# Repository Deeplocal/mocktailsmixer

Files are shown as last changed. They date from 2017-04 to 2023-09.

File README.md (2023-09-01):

# Google Assistant SDK Demo: Mocktails Mixer Gizmology 2023


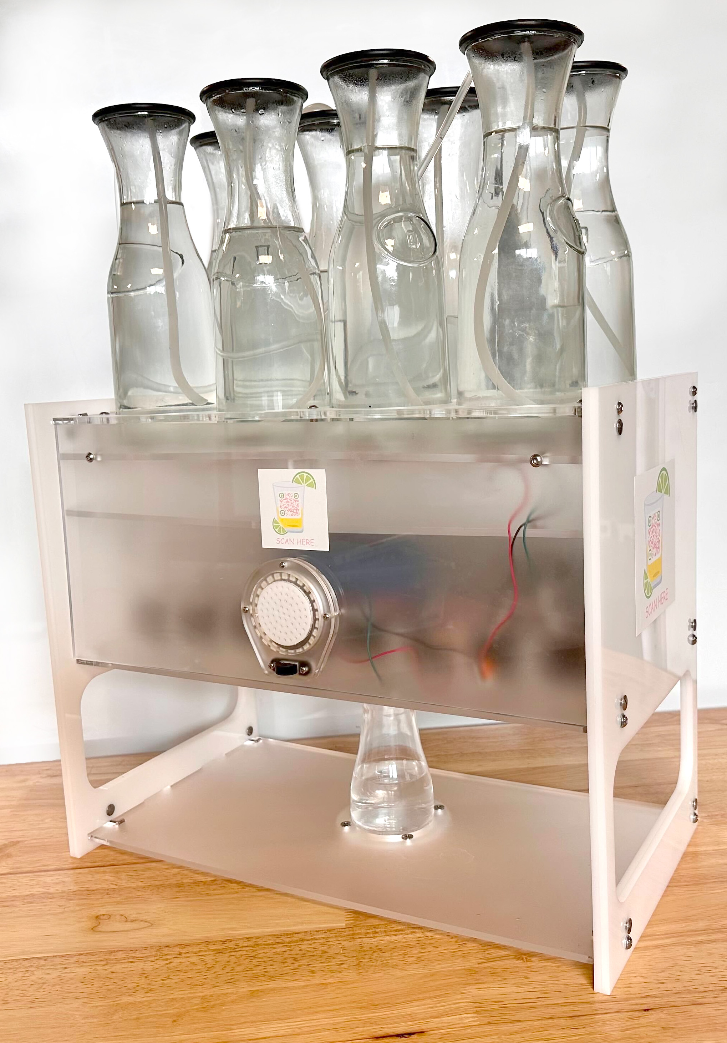
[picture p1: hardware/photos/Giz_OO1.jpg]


## Make a DIY robotic mocktails mixer with the Google Assistant built in.
##In the Spring of 2023, innovation studio and experiential design firm Deeplocal launched Gizmology, a one-year creative technology apprenticeship program for recent high school graduates and underemployed adults in Pittsburgh’s Black community. Supported in part by Deeplocal’s parent company WPP’s racial equity committments, Gizmology’s goal was to advance racial equity in creative and technical fields through on-the-job training and mentorship. Through an initial upfront classroom training spanning nearly four months the Gizmology apprentices, or Gizmos as they affectionately named themselves, learned the foundational skills related to 3D design, electrical engineering, physical computing, fabrication methods (laser cutting/welding/woodworking), and creative technology. Designed as two semesters, Gizmology 1 and Gizmology 2, each semester culminated with a capstone project; the final capstone for the classroom training was to ‘re-create’ a robotic mocktails mixer with Google Assistant built in. 

In mid-July, after weeks of interdisciplinary training and exposure, each of the Gizmos chose an apprenticeship track and set-out to complete the final capstone project fulfilling their specific roles. Jason focused on exhibit fabrication, Jordan delved deeper into technical integration, and Justin focused on Mechanical Design, with each pitching in to work as a team and support the assembly. For Creative Tech, Imani and Mecca shared the responsibility of updating and converting the SDK from Python to Node.Js as it was no longer valid; this was no small feat and an amazing accomplishment for a beginning creative technologist. For all the Gizmos, it was evident that the recreation of the robotic mocktails mixer with Google Assistant wasn’t simply going to be a matter of merely following directions, it was going to take creativity, ingenuity, and most importantly- the real world application of the skills they learned to successfully recreate the project as a team. What you’ll see below is the journey of the Gizmos to create the “Gizmology Mocktails Mixer”, complete with six uniquely designed mocktails (from eight different flavors) representing personal connections to each member of the Gizmology team. This DIY robotic home bartender whips up your favorite mixed drinks at your command–in the true spirit of the Gizmos!

**Disclaimer:** THESE INSTRUCTIONS ARE BEING PROVIDED FOR INFORMATIONAL PURPOSES ONLY AND ARE NOT INTENDED TO BE USED FOR THE PRODUCTION OF COMMERCIAL PRODUCTS.  BY EXECUTING THESE INSTRUCTIONS, YOU AGREE TO ASSUME ALL LIABILITY IN CONNECTION WITH YOUR BUILDING AND USE OF ANY DEVICE. DEEPLOCAL DISCLAIMS ALL WARRANTIES EXPRESS OR IMPLIED WITH RESPECT TO THESE INSTRUCTIONS AND ANY RESULTING DEVICE INCLUDING BUT NOT LIMITED TO WARRANTIES FOR MERCHANTABILITY, FITNESS FOR ANY PARTICULAR PURPOSE, AND NON-INFRINGEMENT.  YOU SHOULD USE EXTREME CAUTION WHEN BUILDING AND USING ANY DEVICE PURSUANT TO THESE INSTRUCTIONS.  IN NO EVENT SHALL DEEPLOCAL BE LIABLE FOR ANY CLAIM OR DAMAGES, INCLUDING BUT NOT LIMITED TO CLAIMS OR DAMAGES RELATED TO DEATH OR PERSONAL INJURY, PROPERTY DAMAGE, OR PRODUCT LIABILITY.

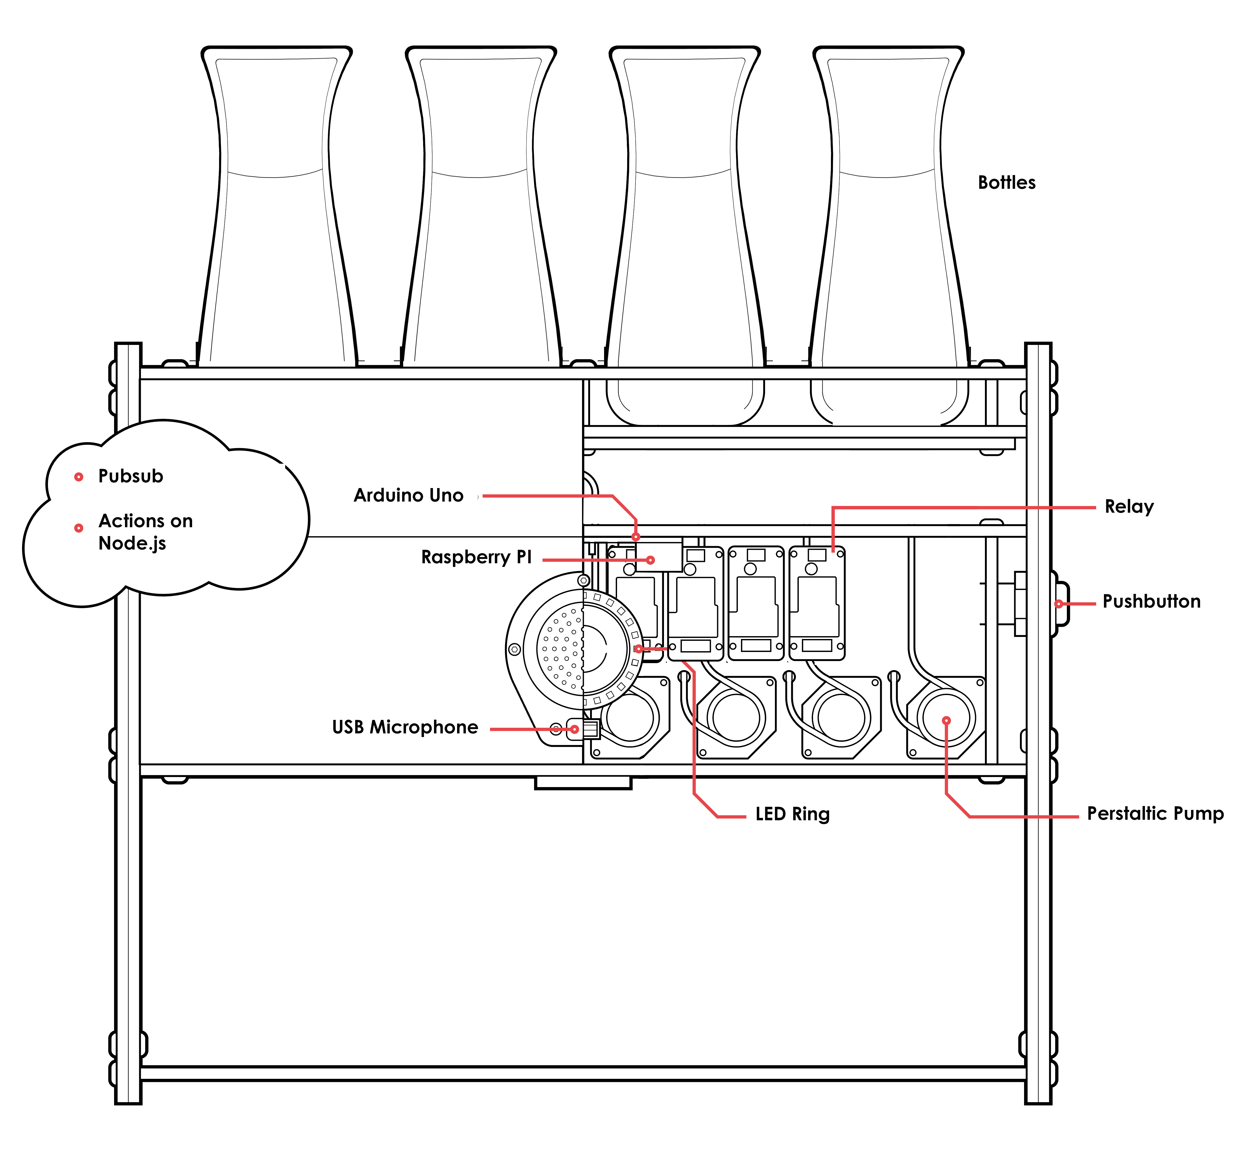
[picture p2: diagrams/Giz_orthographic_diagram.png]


**Features:**

- Voice-controlled drink ordering 
- Modular design allows you to customize your Mixer to include as many ingredients and drink combinations as you choose

## What You’ll Find
- diagrams/
- hardware/
  - cad/
  - laser-cut/
  - photos/
  - bill of materials
- software/
  - arduino/
  - rpi/
  - gcf/
  - api.ai agent zip

## What You'll Need
Before you get started, you should have a basic knowledge of soldering. You should also have access to a laser cutter.
You can find all of the parts we used, along with the exact quantity, supplier, cost, and links to purchase [here](hardware/bom.pdf).
Note: In general, we used parts that were readily available, but on the expensive side. This build could be completed with less expense if parts are sourced on Amazon/Alibaba or if lower quality parts are used.
Note: All materials used in this build are rated as “food safe.” Liquid does not come in contact with any material that is not food grade safe.

### Tools needed for the build are listed below:
- Hand drill
- Rubber mallet or hammer
- Screwdriver set
- X-ACTO knife
- Soldering Iron
- Wire cutters
- Wire strippers
- Scissors
- Hex Key Set
- Wrench Set

## Building the Mixer Body

### Step 1: Laser Cutting
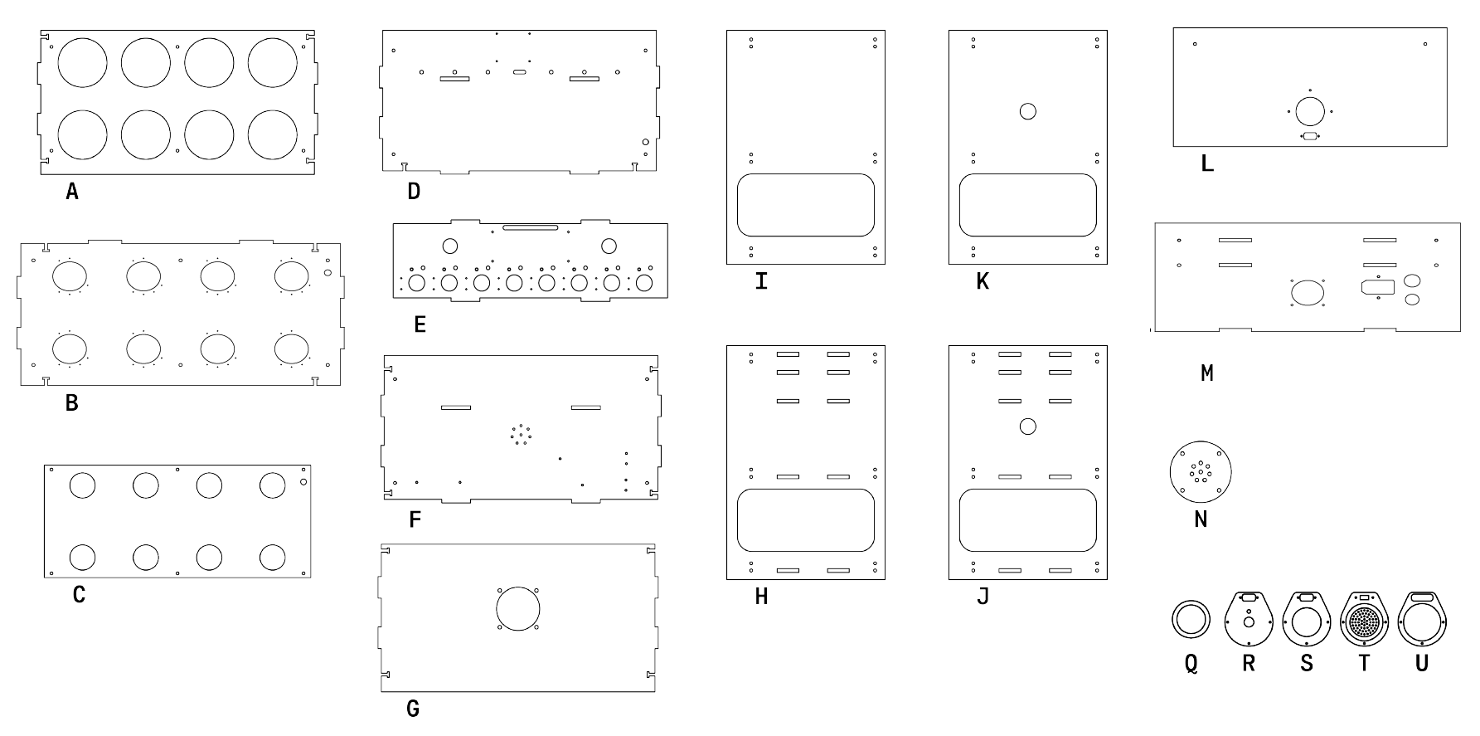
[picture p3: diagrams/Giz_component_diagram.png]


#### Laser cut all 2D profiles into the acrylic sheets.
Note: DFXs are all in inches. Please scale according to input of the laser cutter. See attached drawings for design guidance.
- A. Top Panel- ¼ inch thick
- B. Bottle Capture Panel- ¼ inch thick
- C. Lid Capture Panel- ¼ inch thick*
- D. Drip Panel- ¼ inch thick
- E. Pump-Relay Control Panel- ¼ inch thick*
- F. Pour Panel- ¼ inch thick
- G. Bottom Panel- ¼ inch thick
- H. Inside Side Panel- ¼ inch thick
- I. Outside  Side Panel-¼ inch thick
- J. Inside Side Button Panel-¼ inch thick
- K. Outside SIde Button Panel- ¼ inch thick
- L. Front Panel- ¼ inch thick
- M. Rear Panel- ¼ inch thick*
- N. Cup Indicator Panel- 1/16 inch thick
- O. Arduino Top Plate- 1/16 inch thick 
- P.  Arduino Bottom Plate- 1/16 inch thick
- Q. Speaker Diffusion Level
- R. Speaker Clear Level 16th- 1/16 inch thick
- S. Speaker Black Level 8th- ⅛ inch thick
- T. Speaker Black Level 8th 1- ⅛ inch thick
- U. Speaker Black Level 4th 1- ¼ inch thick

*Panels that were revised include:
Lid Capture Panel- needed holes for the light wire
Pump Relay Control Panel- CAD mount holes for brackets. CAD holes for wires from pumps to power and access for tubes to run through, holes for the relay to be mounted
Rear panel- CAD holes for mounting a fan 

*Note: We highly recomend a cardboard prototype. 

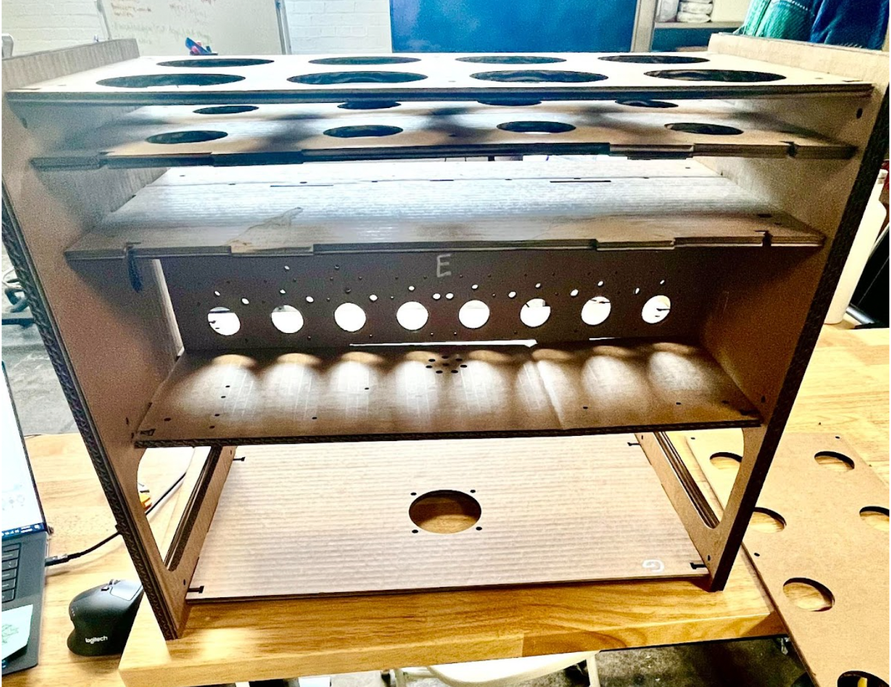
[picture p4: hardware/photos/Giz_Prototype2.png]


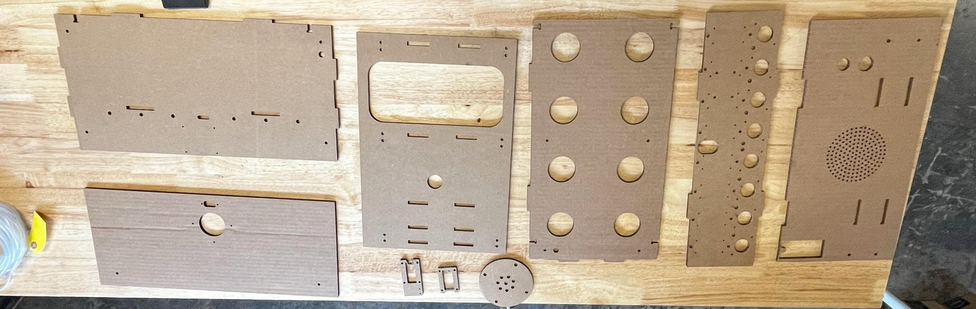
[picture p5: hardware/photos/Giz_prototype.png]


### Step 2: Assemble Bottle Holder Sub
Attach Top Panel with Bottle Capture Panel together with #10-32 x 1/2 inch length button socket cap and #10-32 x 1 inch length ¼ OD standoff.

On the other side, with Lid Capture Panel use 10-32 x ¾ inch length button socket cap fasteners (Optional - Double sided tape can be used to attach the Lid Capture Panel to the bottom of the Bottle Capture Panel).

Note: There is a ¼ inch overhang on the Top Panel. Rear panels are flush with the exception of the tabs.

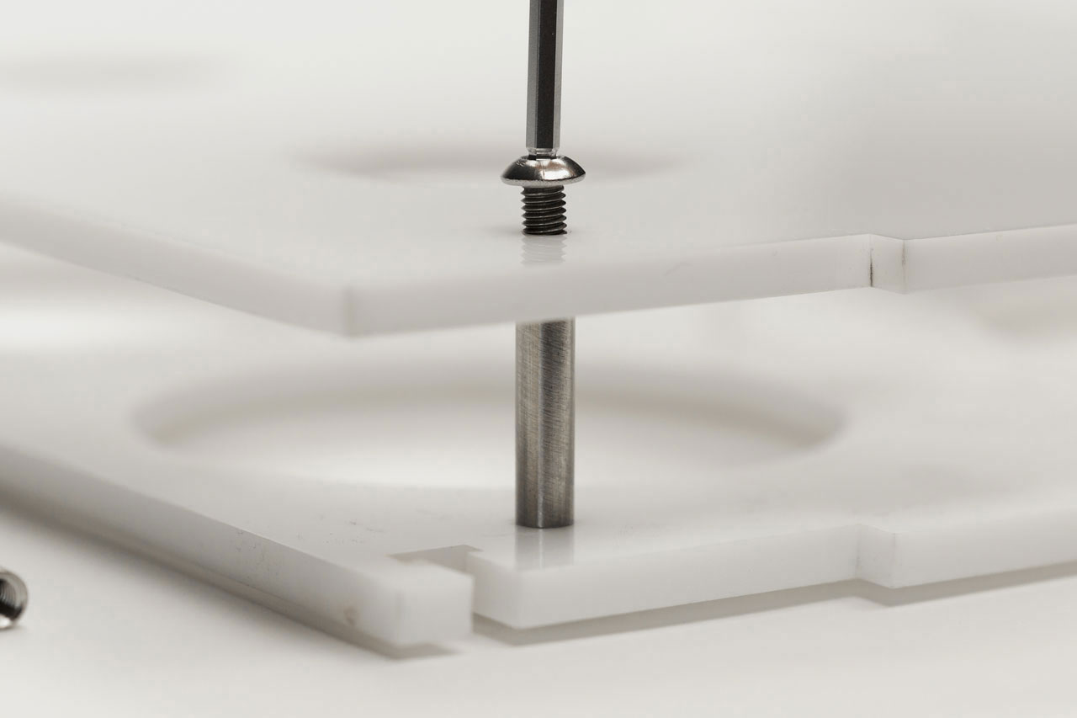
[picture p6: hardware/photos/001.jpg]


### Step 3: Assemble Pump and Relay Control Panel Sub
Note: To ensure pump tubing is food grade safe, please replace with Tygon Clear PVC tubing 3/32 inch ID x 5/32 inch OD (Hardness rating is “Soft” and durometer is 65A). The durometer is imperative to pump and tube life. This can be found on McMaster-Carr.

#### Install Food Grade Pump Tubing.
Remove cover from pumps by depressing snaps on both sides of pump head. Remove tubing that was placed in during shipment. Place food grade tubing into pump allowing 3 inches to remain outside the inlet and outlet of the pump. Also, be careful to not puncture the tubing when installing around the rollers.

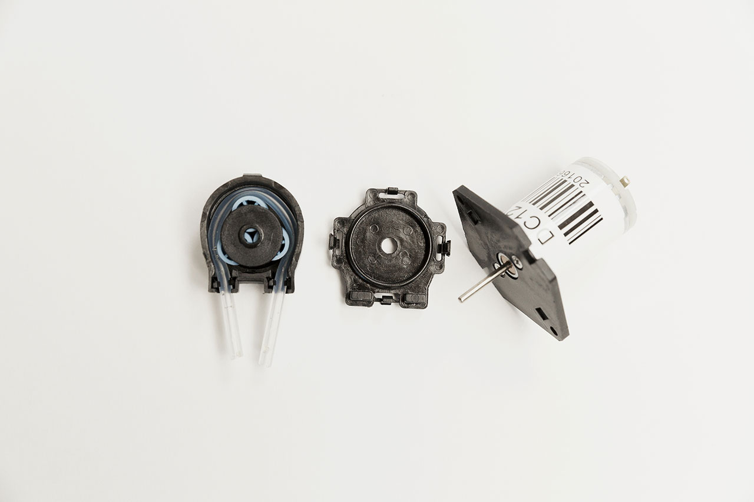
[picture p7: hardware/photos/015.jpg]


#### Attach Pumps.
The pumps that were available required brackets to be mounted. Brackets were created in solidworks and 3D printed. 

Use the Pump/Relay Control Panel and attach the brackets to the eight 1.10 inch diameter holes located on the panel. Place a #8 black rubber washer between the bracket and acrylic to reduce vibration.
Use a #2-56 x ½ inch length Phillips pan head machine screw and corresponding nut to fasten the brackets to the acrylic. Use the same screws and nuts to attach the pump to the bracket.

#### Attach Relay Module.
In this version, to save time, we have used an 8 channel
Relay module. Attach the 8-Channel Relay Module directly above each pump on the Pump/Relay Control Panel. There will be a 4 bolt hole pattern. Use the #2-56 x ⅜ inch length ⅛ inch OD standoffs (Optional - You can use #2-56 x 1/2 inch length Phillips pan head machine screw and corresponding nut instead of the standoffs.) with number #2 washers underneath each hole before the standoff. Fasten each corner with a #2-56 x 5/32 inch length Phillips pan head machine screw.  Note that the red led must be positioned toward the top of the acrylic sheet. Use a #2-56 x ⅜ inch length pan head Phillips machine screw and fasten relays from other side of acrylic.

Tip: When attaching the fasteners, washers and standoffs to the relay module, allow them to be loose. This will help with easy alignment to the corresponding holes on the acrylic than retighten fasteners on relays.

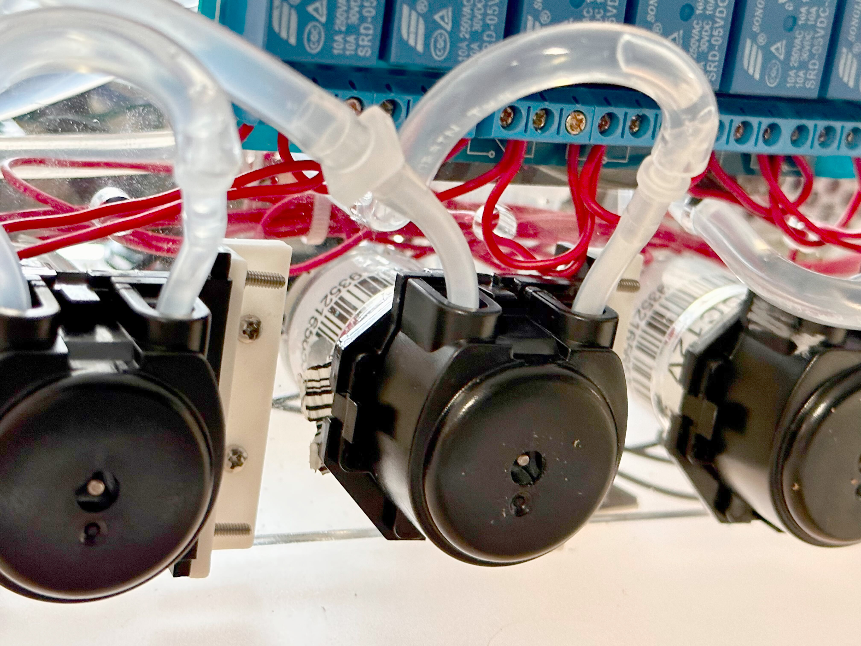
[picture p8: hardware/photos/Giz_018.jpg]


#### Attach Arduino Uno and Arduino Mount.
You can 3D print an Arduino Uno mount by using this link to download the file from GrabCAD. We used a Bambu Studio P1P 3D printer. The file takes about 6 minutes to print in total.

Place the Arduino on the mount, matching the holes on the Arduino to the corresponding holes on the mount. Use screws to secure the Arduino onto the mount. Attach the Arduino and the mount onto the back of the pump panel with VHB. You should leave enough room for the the wires from the relay to come through the slot and attach to the pins on the Arduino Uno.

#### Attach Raspberry Pi to Drip Panel.
Attach the Raspberry Pi to the back panel using velcore. 



## Wiring the Electrical System

#### Electrical System Overview



For a clearer view of the wiring diagram download the [fritzing file](diagrams/wiring_fritzing.fzz).

#### Control
The electrical system of the Mocktails Mixer uses two control systems. The first is a Raspberry Pi, which handles all of the communication with the Google Assistant SDK. The second is an Arduino Micro that controls the pumps and LEDs. Both of these systems are connected to each other over serial. The Raspberry Pi sends commands to the arduino about what lights and pumps to turn on and the Arduino executes them.

Outside of these two controllers, the Mocktails Mixer has four major hardware systems. They are Power, the Pumping system, Lights, and Audio.

#### Power
The power system controls the flow of electricity in the Mixer. However, the Mixer uses two different voltages: 12V for the pumps and 5V for the other hardware. You can handle this by using a step-down voltage regulator or a dual-voltage power supply. These are both adequate for the basic build of the Mixer, but if you want to add extra flair (like more LEDs),  you may need to use two separate power supplies. Our instructions and BOM use two power supplies.

Note: For safety, we recommend placing the power supply in an external enclosure to keep 110V away from the liquids in the mixer.

#### Pumps
In this version of the Mocktails Mixer, we used eight (8) peristaltic pumps. These are rated and recommended for use at 12V, but you can run them up to 24V if you find that the pumps are running too slow. The pumps are all individually switched by a relay controlled by the Arduino Uno.
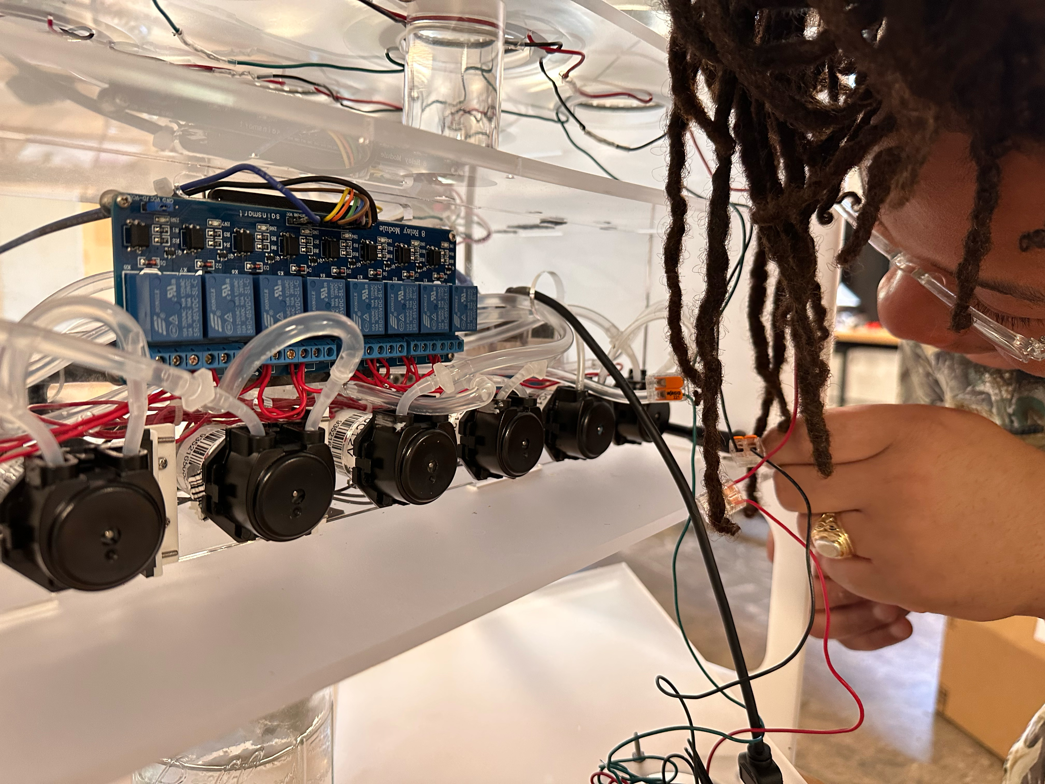
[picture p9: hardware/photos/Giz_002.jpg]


#### Lighting
For visual feedback, we added an LED ring to the Mixer. We used the Adafruit Neopixel. It is very easy to wire and add additional rings, plus the library is easy to use. These draw a decent amount to amperage, so if you want to add more to your build, you will need to size your 5V power supply accordingly.

#### Audio
Last but not least, we used a USB Microphone to speak and order drinks that is connected directly to the Raspberry Pi. We chose to not connect the speaker. If we did, the speaker could be connected to the amplifier on the Arduino’s mounting plate. The amplifier is connected to the Raspberry Pi via a 3.5 mm headphone jack.

## Electrical System Wiring Instructions

### Step 4: Wire the Power Supplies
To wire the power supply, first connect the AC Lines to their terminals (Black to L or Load, White to N or Neutral, Green to Ground). Next, connect the DC power lines to power supplies.
Note: To make the wiring easier to follow, we used red wire for all the 12V lines and green for all of the 5V lines. We kept the all of the Ground wires black because all devices will need to share Ground in order to communicate.
Note: We also recommend using a lower gauge wire (12 or 14 gauge), for the DC power lines moving from the power supply to the terminal block or the wire nut, then using a higher gauge (20 to 24 gauge) for all of the other lines.

Note: The pumps used in this assembly produce a lot of ground noise that can travel throughout the dinrail and could potentially interfere with communication between Raspberry Pi and Arduino to carry out commands properly. It is recommended that you add a 5k capacitor to the dinral with the long side going into the 12V supply and the short side going to ground to store the ground noise and resolve communication interference. 

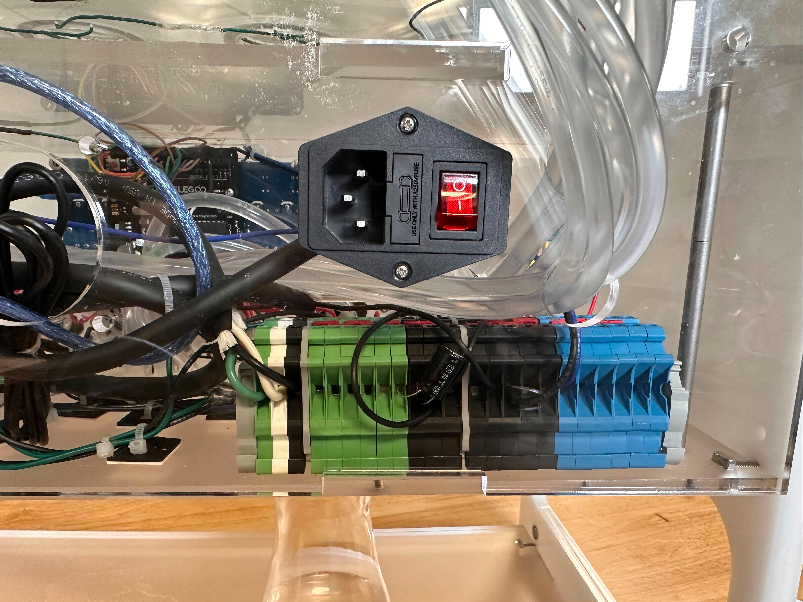
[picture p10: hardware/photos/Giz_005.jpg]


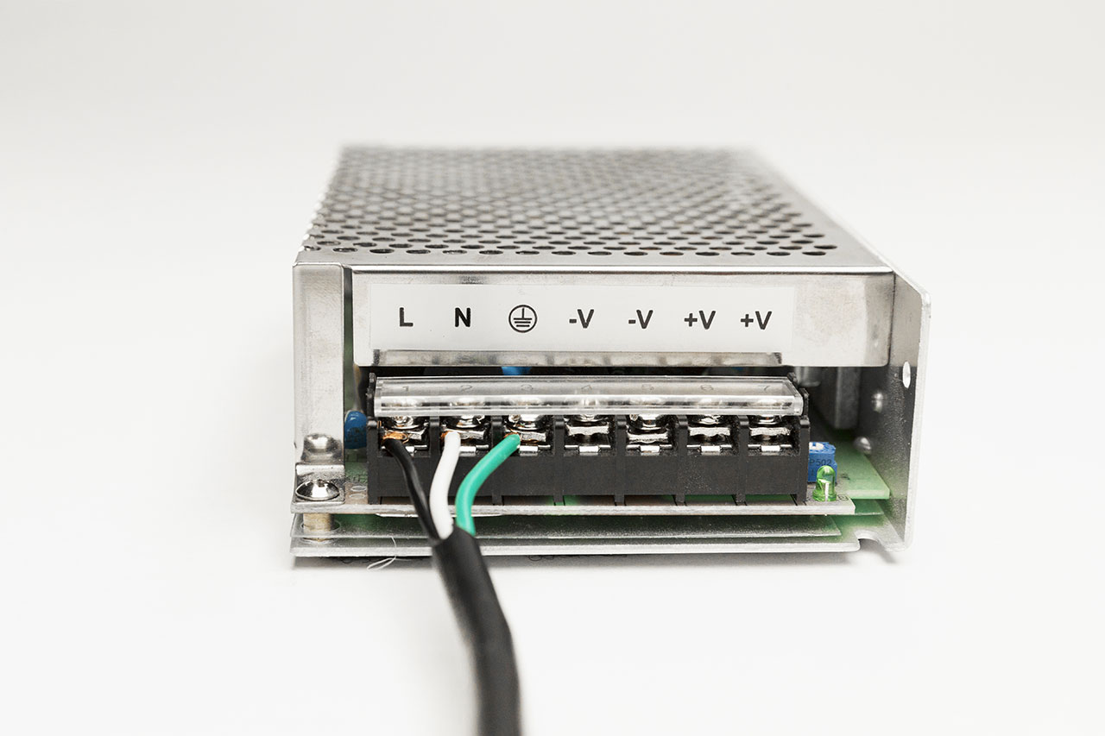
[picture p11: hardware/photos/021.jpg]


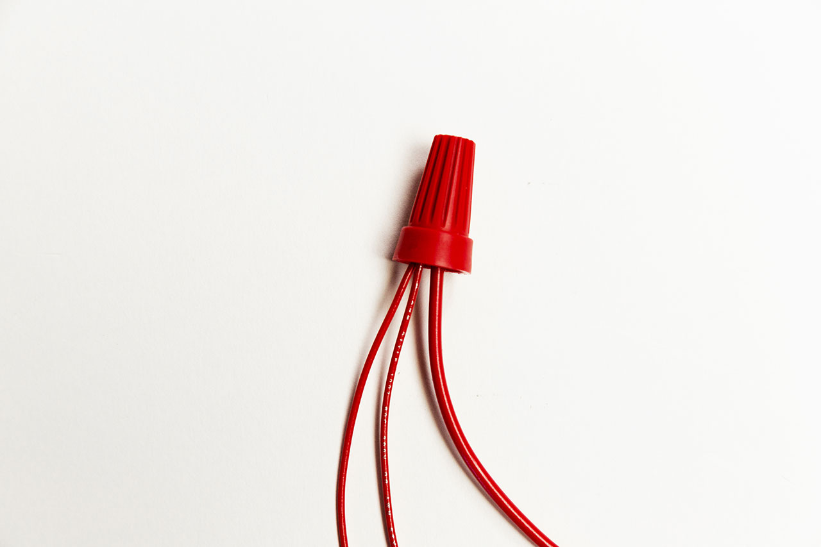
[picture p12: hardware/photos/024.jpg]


### Step 5: Wire the Pumps and Relay Module
Before we start to wire the pumps and relays, first assemble the relay module. We used the SainSmart 8-Channel Relay Module for this build and the assembly instructions for it can be found [here](https://docs.sainsmart.com/article/u1jgnz4x6y-8-channel-5-v-relay-module-resource). We like it because it is easy to use and readily available—but cheaper alternatives are available.
Next, mount all of the pumps and relays to Pump-Relay Control Panel.

Now we are ready to wire the pumps and relay module. First connect the 5V lines to the 5V Terminal on the module. We daisy chained the lines across the relays to reduce the amount of wires going to the main 5V terminal.

Similarly to the 5V power, connect the Ground wires to the GND terminals on the relays, also daisy chaining them.
Next, connect the control lines from the CTRL terminal on their respective pins on the Arduino. To make connecting the control lines to the Arduino easier, we waited until they were all plugged in before we mounted the Arduino; this way we could still read the pin locations on the back or reset the Arduino if necessary.

The pin-outs for the Arduino are:
- Pump 1 Relay to Pin 3
- Pump 2 Relay to Pin 4
- Pump 3 Relay to Pin 5
- Pump 4 Relay to Pin 7
- Pump 5 Relay to Pin 8
- Pump 6 Relay to Pin 9
- Pump 7 Relay to Pin 10
- Pump 8 Relay to Pin 11

Note: Do Not use Pin 6 to trigger a relay. We reserved that pin to control the lights because it is the PWM pin on the Arduino.

To provide power to the pumps, connect the 12V lines to the COM terminal on the relay (also daisy-chained), then connect the Positive (red) terminal of the pump to the NO terminal on the relay.

Finally, to wrap it all up, connect the Ground lines to the Negative terminal on the pump.
Since the four pumps on the right side of the Mixer are mounted in reverse, we need to change the rotation of the pump to also be reversed. To do this, we just switch the Ground line to the Positive terminal and the Power line from the relay to the Negative terminal.

### Step 6: Wire the LEDs

Wiring the NeoPixel LED ring is very easy. Just solder our data line from PIN 6 on the Arduino to the DIN pin, then connect our 5V line to 5V and the Ground line to GND.
If you would like to add more LED rings, all you need to do is wire the DOUT from the first ring to the DIN of the next ring. Then, just connect the 5V and grounds on both rings together.

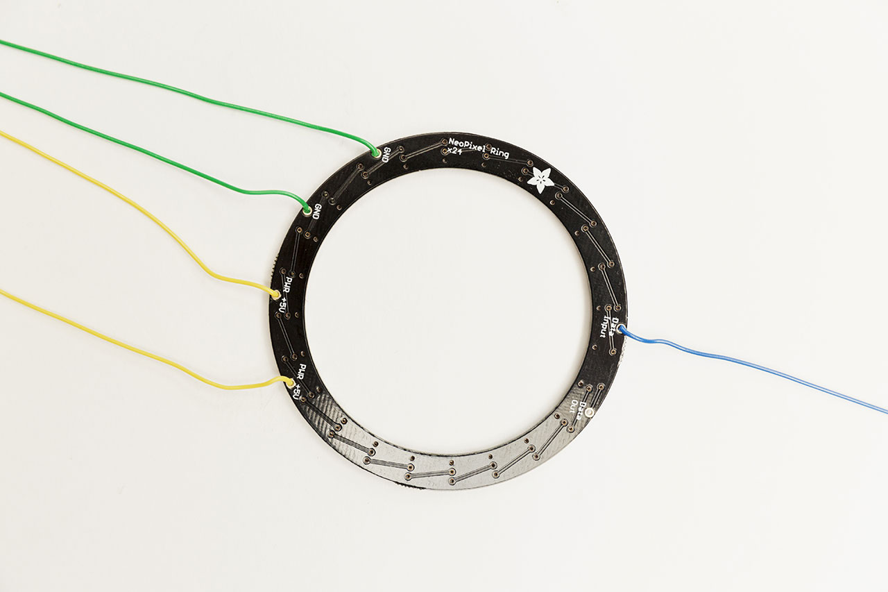
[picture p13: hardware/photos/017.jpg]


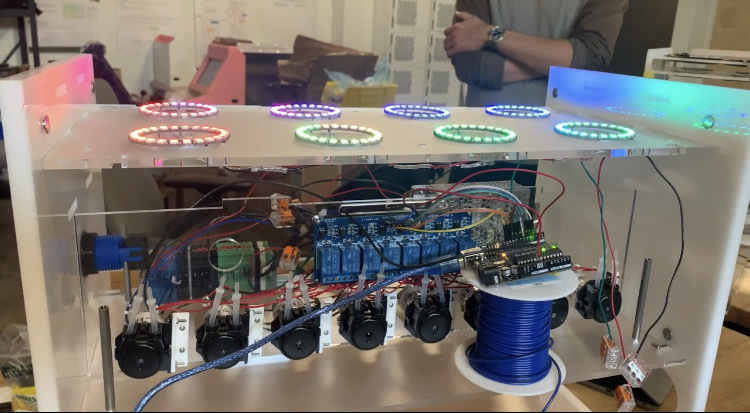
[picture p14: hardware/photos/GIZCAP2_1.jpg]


### Step 7: Wire the Audio
Since the microphone is USB controlled, there is no wiring necessary.

### Final Connections
To power the Raspberry Pi, connect a Ground line to a ground pin on the Pi, then connect a 5V line to the 5V in on the Pi.

To activate the voice command, there is a button on the side for you to push. To wire this button, connect the COM terminal to the 3.3V Out on the Raspberry Pi. Then, connect the NO terminal on the button to the button’s respective GPIO (in our case GPIO 7). For a cleaner signal, connect a resistor between the NO terminal and Ground.

Double check the wiring. Trace all of them from each piece of hardware to their source. Once you feel good about the wiring, go ahead and power up the system. The Raspberry Pi should have a red power light visible and the Arduino should have a blue power light visible as well.

## Building the Mixer Body Continued

### Step 8: Assemble Pump Control Center Sub
Assemble Pump/Relay Control Panel between Drip Panel and Pour Panel with corresponding tabs and slots on each sheet of acrylic. Make sure the pumps and relays that face the front of the unit are in front of the pour holes in the center pour plate.
Use 10-32 standoffs and 10-32 fasteners to bring the sub-assembly together. A #10-32 X ½ inch length of all thread will be used to bring the #10-32 X 2 inch length standoff and #10-32 X 3 inch length standoffs together.

### Step 9: Assemble Side Panel Sub
Attach Outside Side Panel to Inside Side Panel using the #8-32 binding posts (Optional - You can omit these from the build. They help with holding the side panels together while assembling). The flat side of the binding post should face the Inside Side Panel. Six of the binding posts will be used per Side Assembly.
Repeat with Inside Side Button Panel and Outside Side Button Panel. The side panel assembly with the button will be on the right side of the unit when looking at the unit from the front.

### Step 10: Assemble Cup Indication on Bottom Panel
Attach Cup Indicator Panel to Bottom Panel with #8-32 Low Profile Binding Barrels. (Optional - Cup indicator helps a user where to place their cup but is not necessary in the assembly).

### Step 11: Bring all the Sub-Assemblies Together

Begin by laying a Side Assembly on its face with slots facing upwards. This will allow for easy installation of the other components.

Attach Bottle Holder Sub-Assembly to the top of the Side Panel Assembly by aligning the slots. Note that the tabs in the rear must face the rear of the unit.

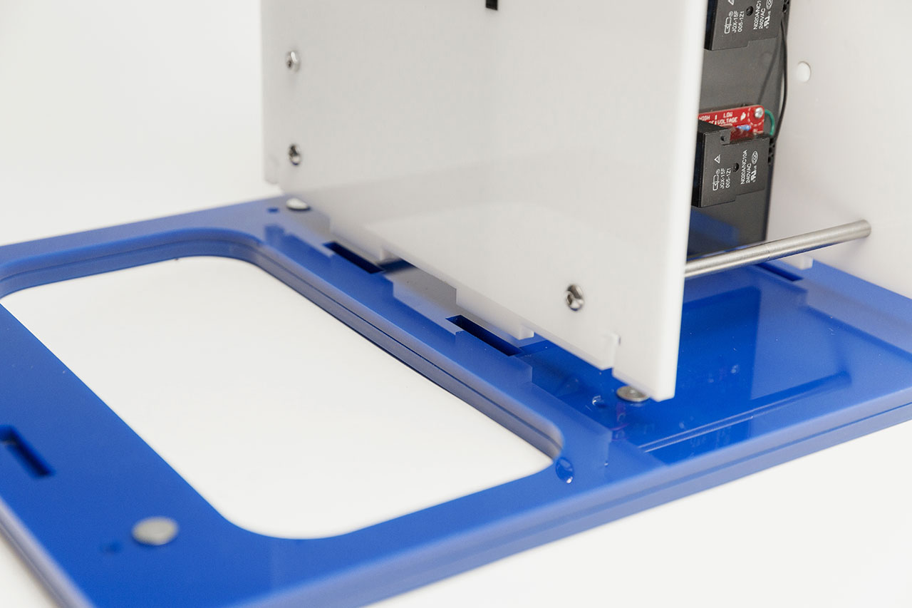
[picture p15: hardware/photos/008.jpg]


Next, attach the Pump/Relay Control Panel Sub-Assembly right below the Bottle Holder Sub-Assembly, noting that the tabs will align like before. Note that the pumps must be facing towards the front of the unit and the electric motor faces the rear. The front of the unit can be determined by the amount of space between the slots and the edge of Side Panels—the larger gap indicates the front of the unit.

Attach the Bottom Panel to the last two remaining slots towards the bottom of the Side Panel Assembly.

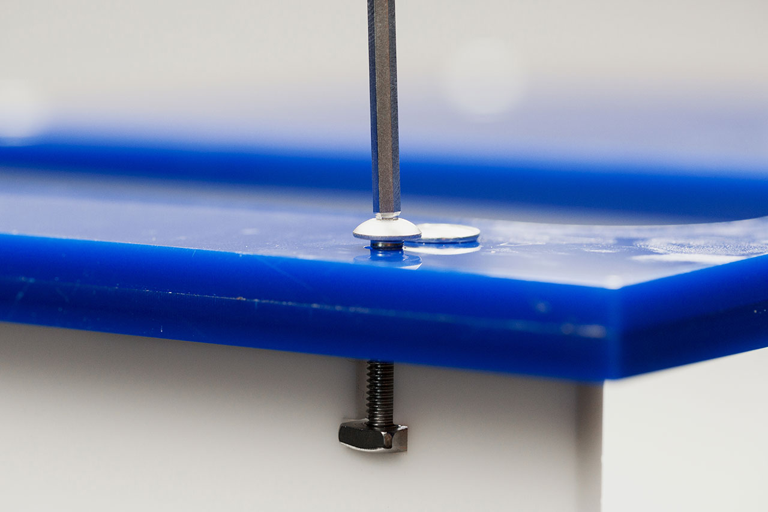
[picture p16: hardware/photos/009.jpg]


Attach the other Side Panel Assembly, mating all tabs and slots. Use the #10-32 X 1 inch length button socket cap and corresponding square nuts to secure the unit. There are six of these per side.

Rotate the unit 180 degrees and fasten the other six fasteners. Tip: Be careful when rotating the unit and make sure to firmly hold the two side panel assemblies together. A second person may be helpful here.

### Step 12: Cut and Fit Fluid Delivery Tubes to Length and Install
Begin by taking the ¼ inch OD tubing (food safe) and run it from each pump up through the holes in the Drip Panel. Leave an additional 8-10 inches of extra tubing to easily remove a bottle.

Next using the tube connectors run the ¼ inch OD tubing (food safe) from the pump outlet to the pour holes in the center of the Pour Panel. The tubes will fit snuggly in each of the 8 holes. They are made to have a slight interference fit.

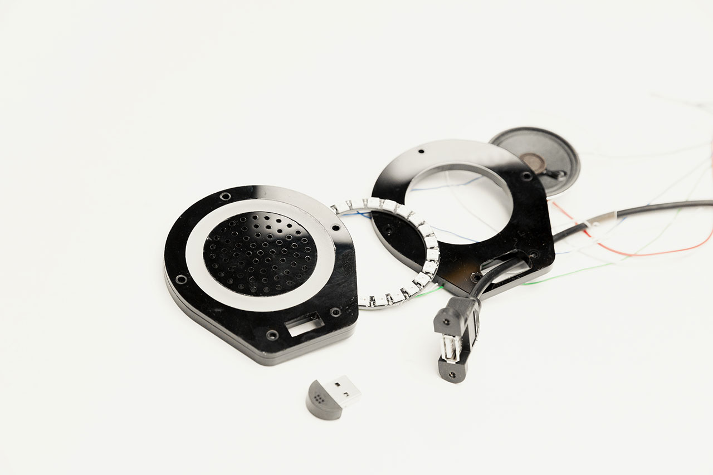
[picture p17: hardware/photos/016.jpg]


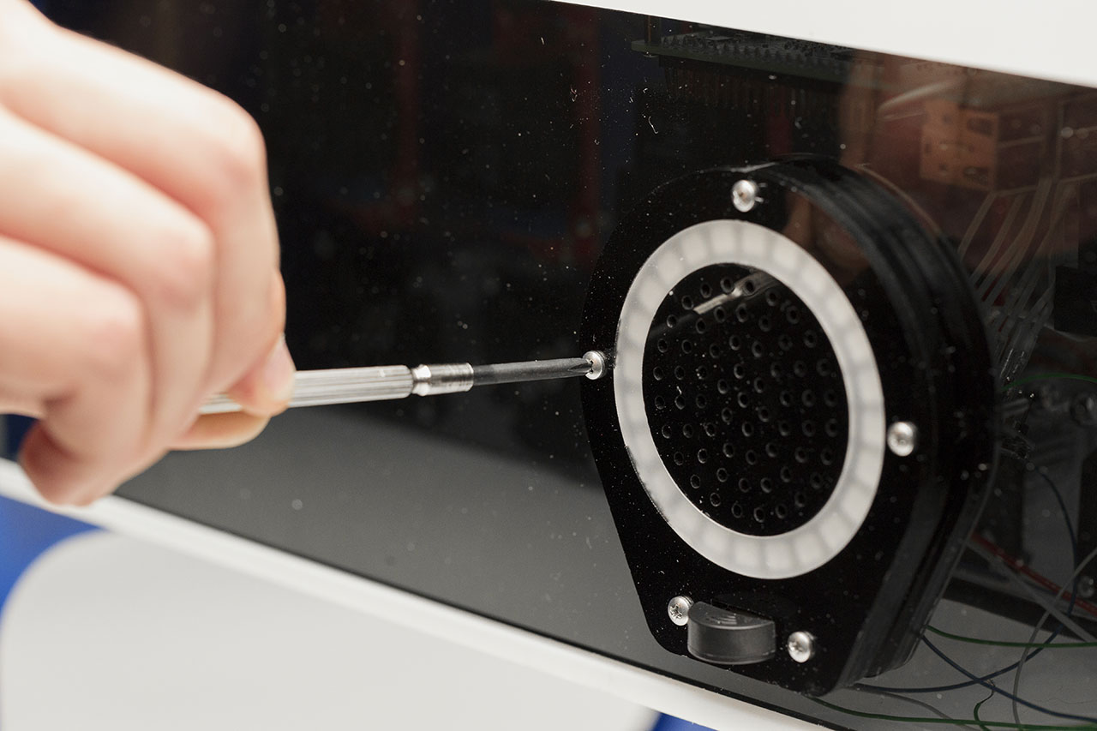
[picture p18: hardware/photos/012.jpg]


### Step 13: Attach Front Panel to Unit
Attach Front Panel to unit with 10-32 x ¾ inch length button socket cap and corresponding square nuts. There are two of these that hold the panel in place.
Tip: Use a piece of Painters tape to hold the square nuts in place until fasteners grab. Tape can be removed after through the bottle holes.

### Step 14: Attach Rear Panel to Unit
Align the Rear Panel with the corresponding slots and tabs on the rear of the unit. Once again, use the #10-32 x ¾ inch length button socket cap and respective square nuts.

## Bottle Build

### Step 15: Drill hole for tube connectors
In the lids to the carafe, drill a 1/4 inch hole for tubing. 

### Step 16: Place Bottle Assembly into Unit
Fill bottles with desired liquid, place on top of the mixer, put the lid on each carafe, feed the tubing throught the hole all the way to the bottom of the carafe. 

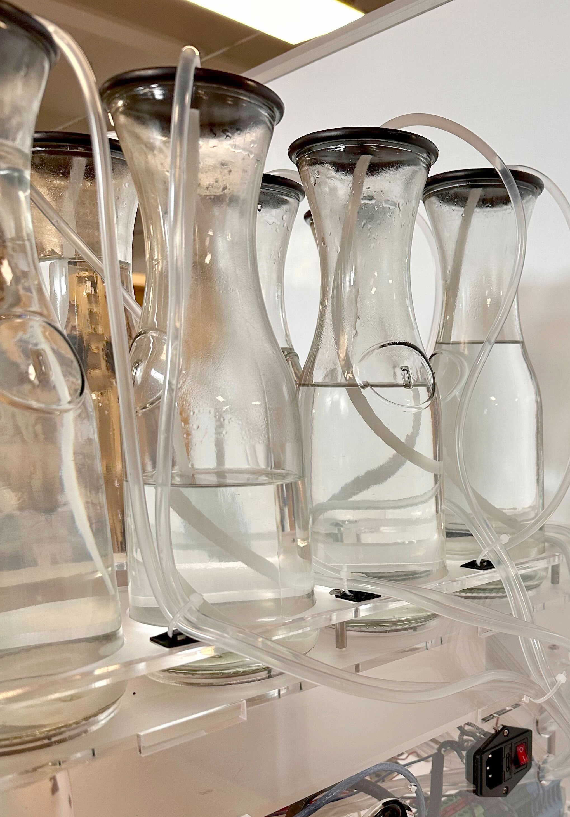
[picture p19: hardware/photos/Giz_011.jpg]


## Programming the Mixer

### Step 17: Run Javascript Program

#### Install node packages: 
‘Serialport’

‘Speech-to-text’

#### Defining Path and Variables

Declare port as new Serialport and define the path that will be used.

Upload JS program to raspberry pi and ssh into pi to initiate the program and to update the code.

Declare a variable called (‘keyword’) and set it as an empty string.

#### Initiating Program

Ssh into Pi with ssh username and password using git bash.

Type command ‘pm2 restart 0’ to refresh the program.

Cd into  ~/src/mocktailsmixer/software/rpi.

Type command ‘pm2 start index.js’ to run the program.

Type command ‘pm2 logs 0’ to view logs and observe what is happening as the program runs.

The user presses the physical button on the assembled Mocktail Mixer which triggers a serial message to be sent from Arduino to the JavaScript application

#### How Arduino sends a message to the JS program a.k.a. Button Press

A function called handleSerial() listens for a complete serial message from the Arduino to know when to parse a command.

Completed serial messages held in the variable ('data') which contains the string “button” is received from the Arduino and will be passed onto the function buttonCallBack().

Within the buttonCallBack() function there is an if statement that has the condition to use the toString() method to transfer data from the arduino into a string, and the startsWith() method to detect if “button” message has been received by the JS program. If found, it begins recording and sets a timeout for processing.

#### Speech to Text

The JavaScript application picks up the serial message through the function processTranscript() which starts streaming the audio from Speech-to-text API  with settimeout incorporated within the function to start/stop the audio recording for 10 seconds > translated to 10000 milliseconds, then the audio is transcribed.

Once the transcript is processed we then loop through an array of keywords that correspond with the drink names we have, i.e [‘mango’, ‘mechanical’, ‘mud’]  and if detected within the transcript we then calculate how many seconds each relay should be turned on and transmit those commands to arduino via serial.

#### How does the JS Program communicate to the arduino?

The buttonCallback() function calls the function keyWordToArduino(‘keyword’)  for 10,000 milliseconds, else it responds with a console.log(“don’t know that one”) 

The keyWordToArduino function has a series of if statements that will open and close the relays of each bottle depending on the correct keyword being detected.

The initial if statement will use the include() method to check if the variable 'keyword' includes a chosen keyword like 'mango' for example.
When the word 'mango' is detected, the executed code will include the port.write() method to send a string message to the arduino via serial port to open the first relay. Ex: port.write("b0r!");

Arduino Serial Commands:

          	b= bottle action
           
          	0-7 =index of bottles 
           
              r = on
              
          	l = off
           
            ! = termination
            
      a= active interaction
      
      o = off
      
Each port.write() method must have only one serial command in order to be received by arduino. Ex: to turn on and off relay number one looks like:

 port.write("b0r!")
 
 port.write("b0l!")

Once the first relay is open, a timeout is set to open the next relay after 1 second of the first relay being open. If you open the relays simultaneously the arduino will fail to turn either relay on because there are too many commands at one time, the 1 second setTimeOut is to avoid this problem.

After both relays are open, use the setTimeOut function to close the first relay after the number of seconds it takes to pour the proper ratio based on the drink ingredients. Nested within this setTimeOut there should be another setTimeOut that turns off the second relay after 1 second of the first relay being turned off if it is a 1:1 ratio or the proper number of milliseconds that is required based on specific drink ratios. 

For the remaining keywords, else if statements are used that follow the above pattern in the keyWordToArduino function.

An else statement is used to tell the user to try again if no keywords were detected.

Within the handleSerial() function there is a port.write(“a!”) command which communicates to the Arduino that the button press was received by the JS program and it will not allow any new button press commands to be received until the entire program has run and been completed.

### Step 18: Prepare Arduino
- Load sketch onto board.
- Connect to Raspberry Pi via USB.

### Step 19: Run system

SSH into the pi with ssh dluser@10.0.7.197 and password deeplocal if that fails, plug and hdmi into the board and connect it to a monitor, and the board should show a grey screen with white text that shows its current IP address. It should auto-connect to devtest on boot (it has been so far)
check if pm2 is running with pm2 l which should list the current processes that are running. If it's already running you can restart it with pm2 restart 0 or watch the logs with pm2 logs 0 , but if it's not running you need to cd ~/src/mocktailsmixer/software/rpi and then pm2 start index.js (and then you can view the logs to see what's happening with pm2 logs 0



## Step 20: Order you Drink

Scan the QR code to find a list of drinks available. 

Prep your glass as desired, place in the cup holder.

Push the button on the side to active.

Ask for your drink of choice.

[](diagrams/MIXER_QR.png)

[](diagrams/GIZmocktailMENUFinal.png)

## Cleaning Your Mixer

- After use, empty your bottles from earlier contents and rinse with water.
- Fill each bottle with water and run Mixer to clean lines of any residue that may be left behind. This will keep the Mixer clean and ready for the next time you change liquids.
- Run the Mixer pumps until no liquid can be seen coming out. This will ensure no liquid is left in the lines.
- Remove bottles from Mixer and allow them to dry after rinsing them out.
- Periodically check all hoses and connections to prevent leaks from developing.

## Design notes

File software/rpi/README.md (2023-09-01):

# Mocktails Mixer Software

> Software that lives on the raspberry pi computer

<!-- [TODO AREN & EMMANUEL] -->

### Goals of this project
- Stay within the RPI directory

- Connect a microphone stream to the Google Speech-to-Text external API

- Configure bottle number, pour-time and light triggering for each drink 

- Have a detected word trigger one of 3 messages to be sent over serial. 

- Hand-off to integration for Arduino code
### Todos (in steps)

1. gcloud permissions or key management with a service account

1. Use 'speech' file to transcribe our audio, using node-record-lpcm-16 library. 

1. Start and Stop recording on command 

1. Start and Stop Recording on external button press

1. Separate one 'keyword' from 'transcript', and check if it is one of the 3 flavors in 'dialog'

1. If one of the words in the transcript is a flavor name, send a message over serial to the Arduino mini to make one of the three drinks.
    - [serialport](https://serialport.io/docs/guide-installation#raspberry-pi-linux)

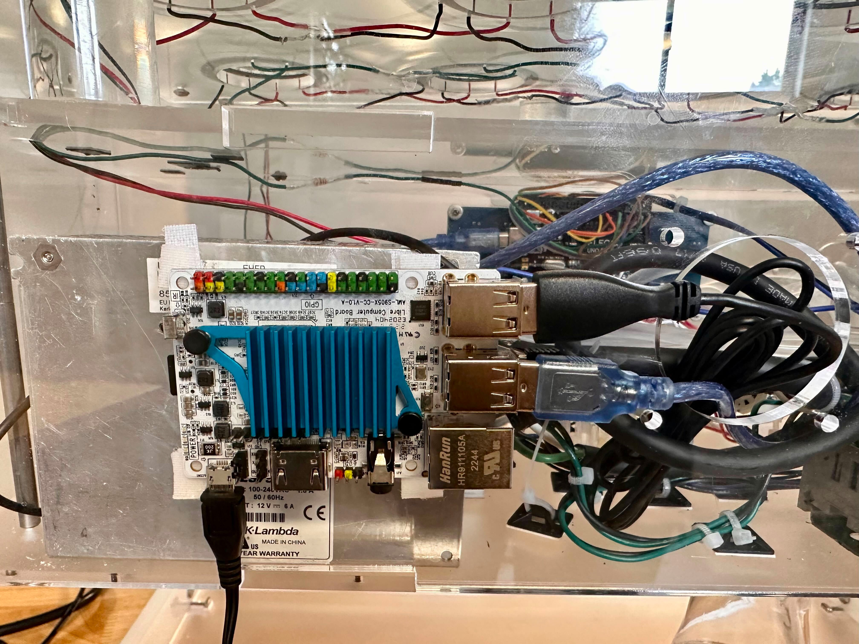
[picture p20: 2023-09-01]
hardware/photos/Giz_025.jpg

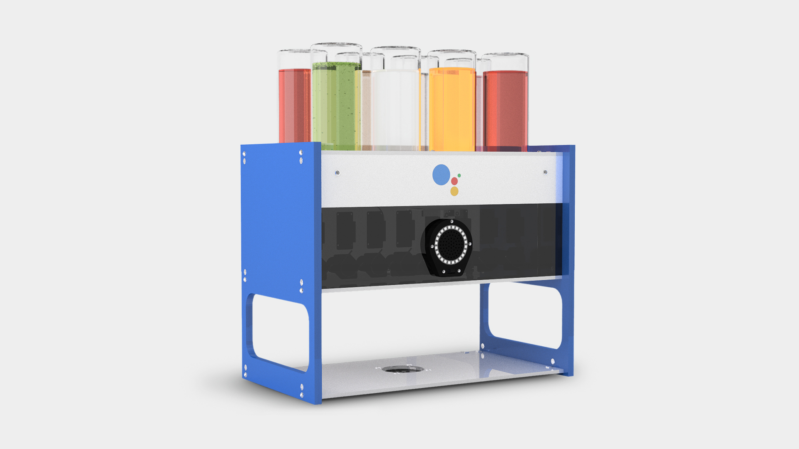
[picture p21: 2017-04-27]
hardware/photos/hero.jpg

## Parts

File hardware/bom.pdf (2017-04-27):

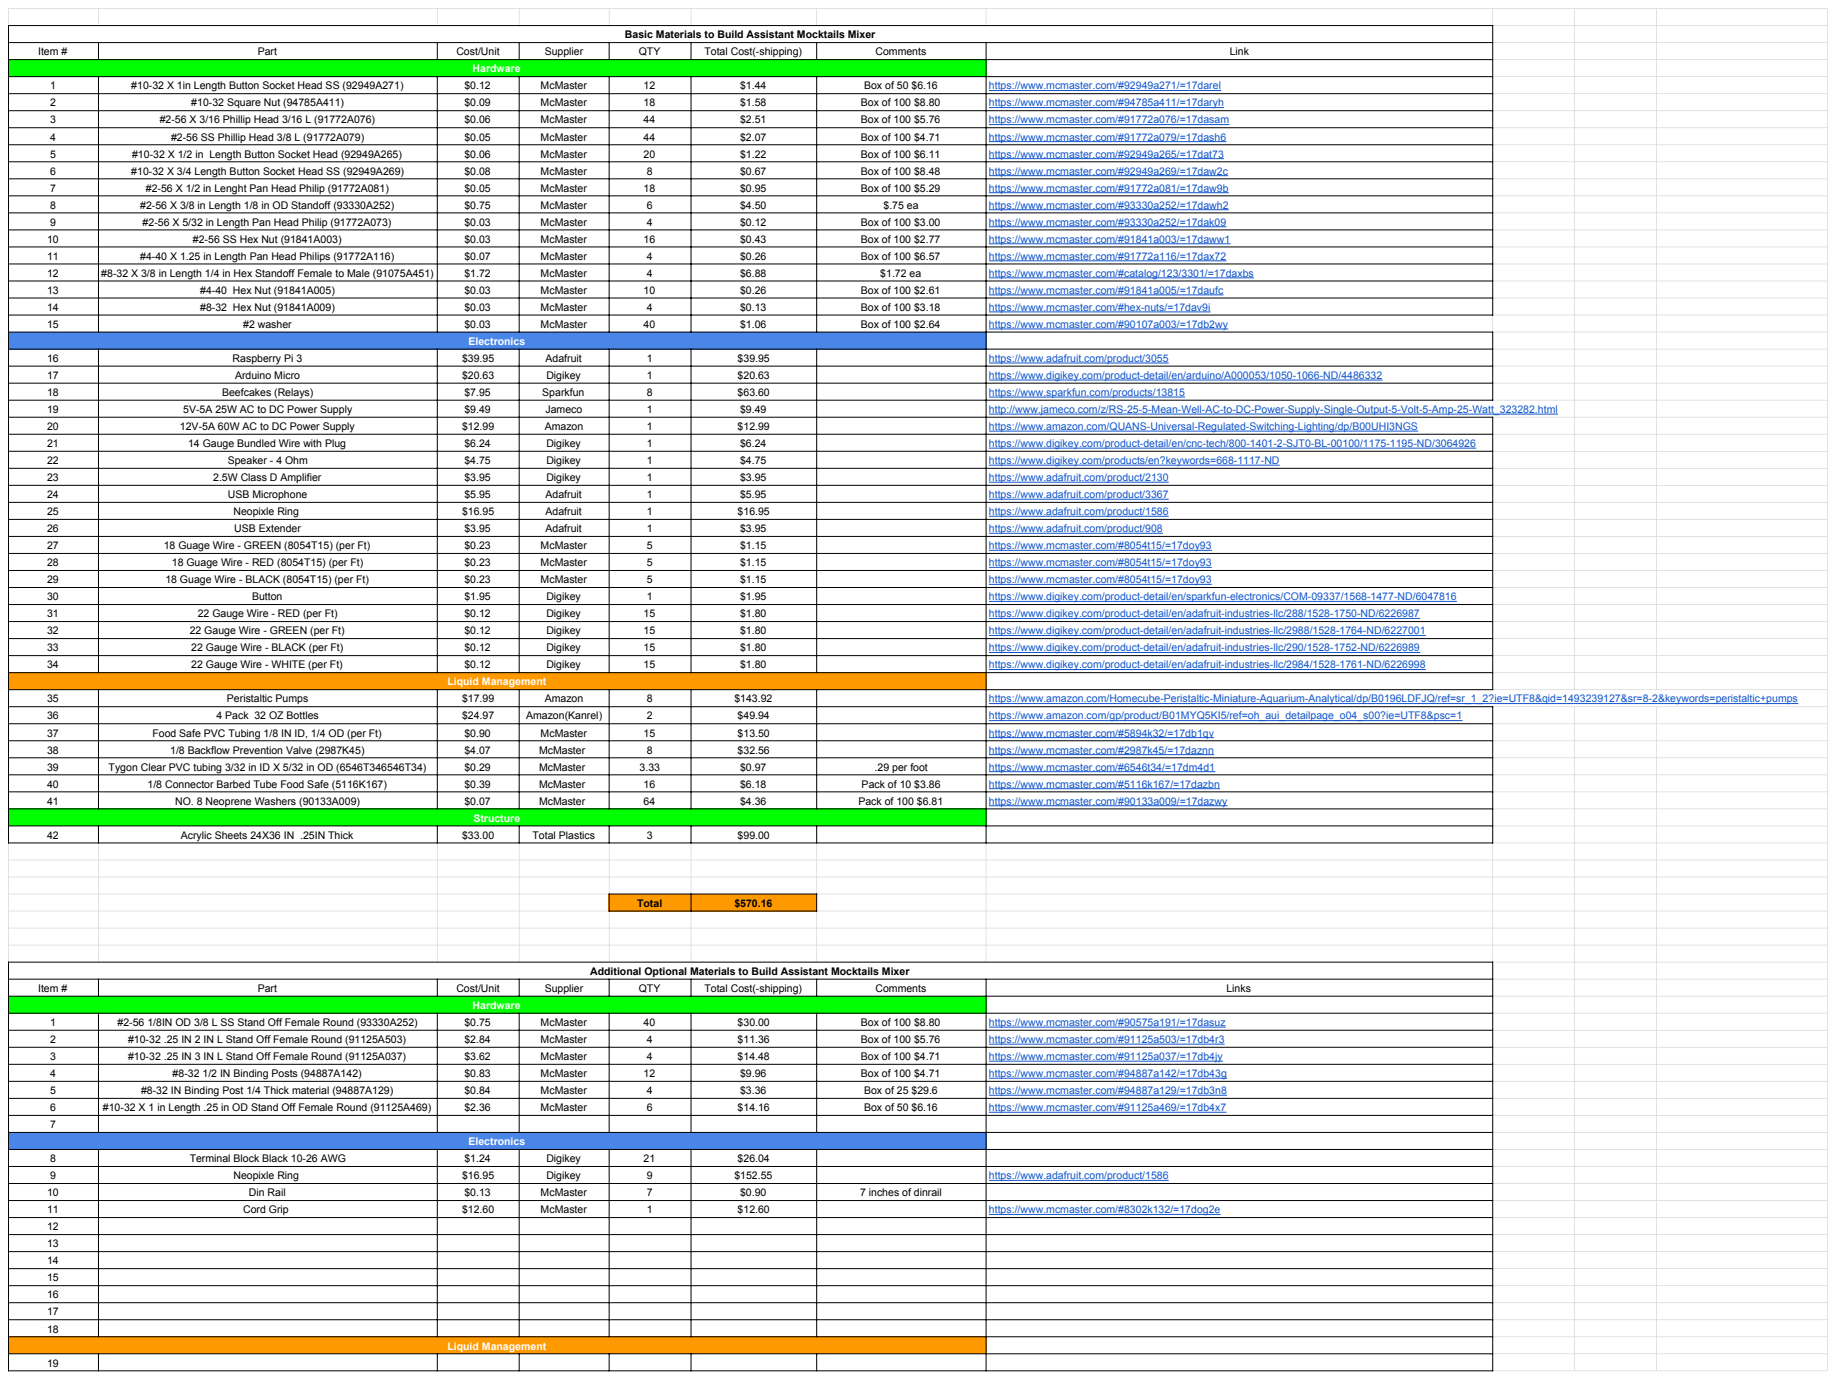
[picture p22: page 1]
Item #; Part; Cost/Unit; Supplier; QTY; Total Cost(-shipping); Comments; Link Hardware; #2 washer; McMaster; Box of 100 $2.64; https://www.mcmaster.com/#90107a003/=17db2wy; 5V-5A 25W AC to DC Power Supply; Jameco; http://www.jameco.com/z/RS-25-5-Mean-Well-AC-to-DC-Power-Supply-Single-Output-5-Volt-5-Amp-25-Watt_323282.html; Peristaltic Pumps; Amazon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

Basic Materials to Build Assistant Mocktails Mixer

1 | #10-32 X 1in Length Button Socket Head SS (92949A271) | $0.12 | McMaster | 12 | $1.44 | Box of 50 $6.16 | https://www.mcmaster.com/#92949a271/=17darel
2 | #10-32 Square Nut (94785A411) | $0.09 | McMaster | 18 | $1.58 | Box of 100 $8.80 | https://www.mcmaster.com/#94785a411/=17daryh
3 | #2-56 X 3/16 Phillip Head 3/16 L (91772A076) | $0.06 | McMaster | 44 | $2.51 | Box of 100 $5.76 | https://www.mcmaster.com/#91772a076/=17dasam
4 | #2-56 SS Phillip Head 3/8 L (91772A079) | $0.05 | McMaster | 44 | $2.07 | Box of 100 $4.71 | https://www.mcmaster.com/#91772a079/=17dash6
5 | #10-32 X 1/2 in Length Button Socket Head (92949A265) | $0.06 | McMaster | 20 | $1.22 | Box of 100 $6.11 | https://www.mcmaster.com/#92949a265/=17dat73
6 | #10-32 X 3/4 Length Button Socket Head SS (92949A269) | $0.08 | McMaster | 8 | $0.67 | Box of 100 $8.48 | https://www.mcmaster.com/#92949a269/=17daw2c
7 | #2-56 X 1/2 in Lenght Pan Head Philip (91772A081) | $0.05 | McMaster | 18 | $0.95 | Box of 100 $5.29 | https://www.mcmaster.com/#91772a081/=17daw9b
8 | #2-56 X 3/8 in Length 1/8 in OD Standoff (93330A252) | $0.75 | McMaster | 6 | $4.50 | $.75 ea | https://www.mcmaster.com/#93330a252/=17dawh2
9 | #2-56 X 5/32 in Length Pan Head Philip (91772A073) | $0.03 | McMaster | 4 | $0.12 | Box of 100 $3.00 | https://www.mcmaster.com/#93330a252/=17dak09
10 | #2-56 SS Hex Nut (91841A003) | $0.03 | McMaster | 16 | $0.43 | Box of 100 $2.77 | https://www.mcmaster.com/#91841a003/=17daww1
11 | #4-40 X 1.25 in Length Pan Head Philips (91772A116) | $0.07 | McMaster | 4 | $0.26 | Box of 100 $6.57 | https://www.mcmaster.com/#91772a116/=17dax72
12 | #8-32 X 3/8 in Length 1/4 in Hex Standoff Female to Male (91075A451) | $1.72 | McMaster | 4 | $6.88 | $1.72 ea | https://www.mcmaster.com/#catalog/123/3301/=17daxbs
13 | #4-40 Hex Nut (91841A005) | $0.03 | McMaster | 10 | $0.26 | Box of 100 $2.61 | https://www.mcmaster.com/#91841a005/=17daufc
14 | #8-32 Hex Nut (91841A009) | $0.03 | McMaster | 4 | $0.13 | Box of 100 $3.18 | https://www.mcmaster.com/#hex-nuts/=17dav9i

Electronics

16 | Raspberry Pi 3 | $39.95 | Adafruit | 1 | $39.95 | https://www.adafruit.com/product/3055
17 | Arduino Micro | $20.63 | Digikey | 1 | $20.63 | https://www.digikey.com/product-detail/en/arduino/A000053/1050-1066-ND/4486332
18 | Beefcakes (Relays) | $7.95 | Sparkfun | 8 | $63.60 | https://www.sparkfun.com/products/13815

20 | 12V-5A 60W AC to DC Power Supply | $12.99 | Amazon | 1 | $12.99 | https://www.amazon.com/QUANS-Universal-Regulated-Switching-Lighting/dp/B00UHI3NGS
21 | 14 Gauge Bundled Wire with Plug | $6.24 | Digikey | 1 | $6.24 | https://www.digikey.com/product-detail/en/cnc-tech/800-1401-2-SJT0-BL-00100/1175-1195-ND/3064926
22 | Speaker - 4 Ohm | $4.75 | Digikey | 1 | $4.75 | https://www.digikey.com/products/en?keywords=668-1117-ND
23 | 2.5W Class D Amplifier | $3.95 | Digikey | 1 | $3.95 | https://www.adafruit.com/product/2130
24 | USB Microphone | $5.95 | Adafruit | 1 | $5.95 | https://www.adafruit.com/product/3367
25 | Neopixle Ring | $16.95 | Adafruit | 1 | $16.95 | https://www.adafruit.com/product/1586
26 | USB Extender | $3.95 | Adafruit | 1 | $3.95 | https://www.adafruit.com/product/908
27 | 18 Guage Wire - GREEN (8054T15) (per Ft) | $0.23 | McMaster | 5 | $1.15 | https://www.mcmaster.com/#8054t15/=17doy93
28 | 18 Guage Wire - RED (8054T15) (per Ft) | $0.23 | McMaster | 5 | $1.15 | https://www.mcmaster.com/#8054t15/=17doy93
29 | 18 Guage Wire - BLACK (8054T15) (per Ft) | $0.23 | McMaster | 5 | $1.15 | https://www.mcmaster.com/#8054t15/=17doy93
30 | Button | $1.95 | Digikey | 1 | $1.95 | https://www.digikey.com/product-detail/en/sparkfun-electronics/COM-09337/1568-1477-ND/6047816
31 | 22 Gauge Wire - RED (per Ft) | $0.12 | Digikey | 15 | $1.80 | https://www.digikey.com/product-detail/en/adafruit-industries-llc/288/1528-1750-ND/6226987
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

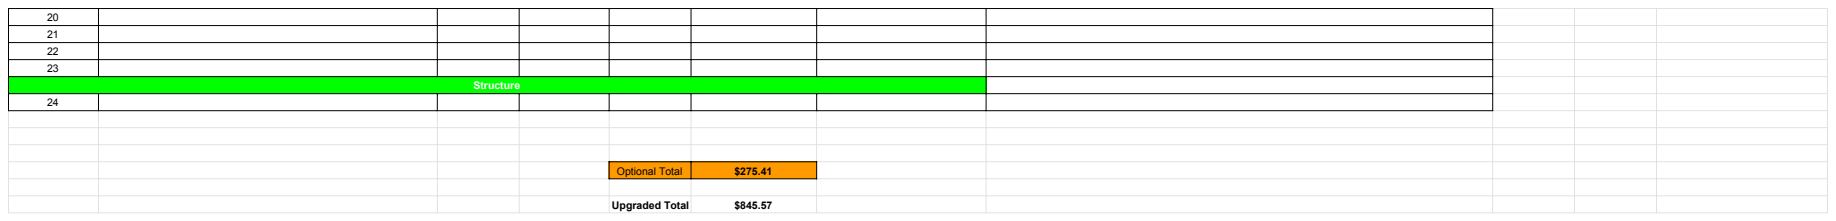
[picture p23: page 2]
Optional Total; Upgraded Total

20
21
22
23

Structure

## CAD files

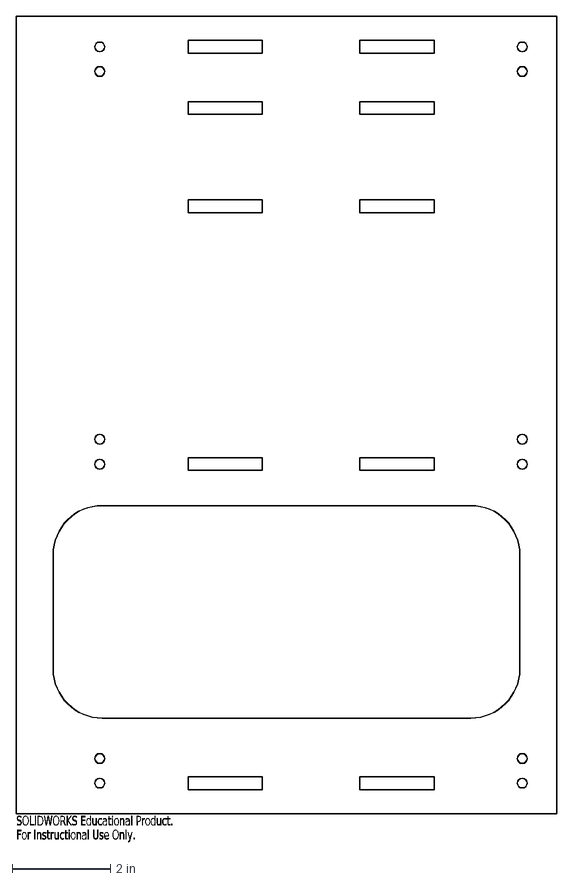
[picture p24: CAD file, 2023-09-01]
hardware/laser-cut/NEW FILES/Inside_side_panel CAP 2.DXF
SOLIDWORKS Educational Product.
For Instructional Use Only.

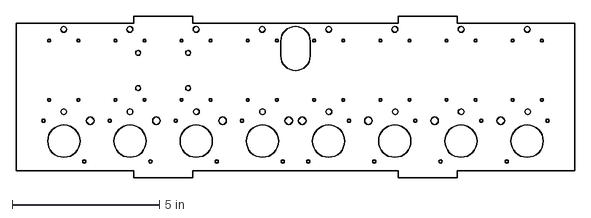
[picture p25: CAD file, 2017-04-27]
hardware/laser-cut/pump_relay_control_panel.DXF
19.0 x 5.50 in

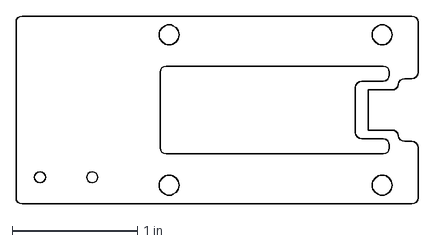
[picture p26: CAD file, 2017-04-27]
hardware/laser-cut/arduino_bottom_plate.DXF
3.21 x 1.50 in

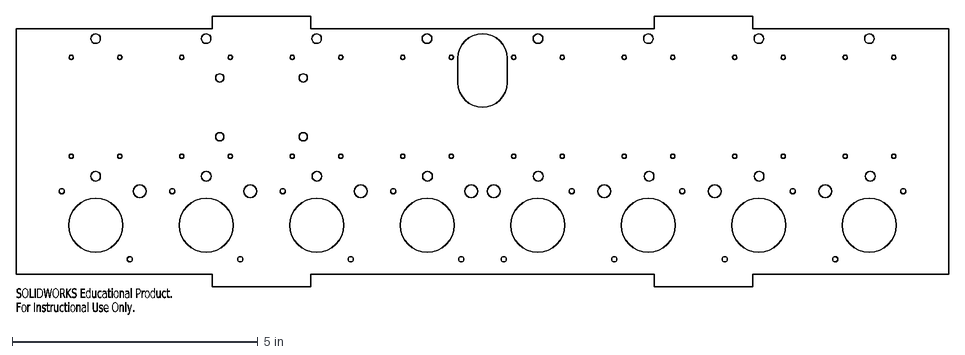
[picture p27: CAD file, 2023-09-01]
hardware/laser-cut/NEW FILES/Pump Relay Control Panel CAP 2.DXF
SOLIDWORKS Educational Product.
For Instructional Use Only.

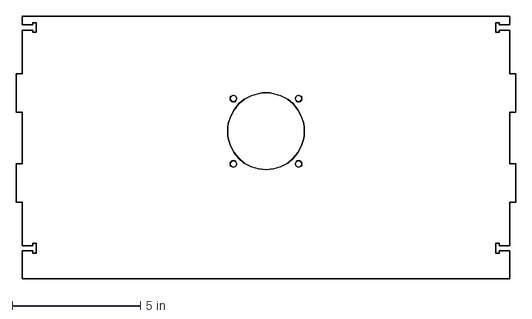
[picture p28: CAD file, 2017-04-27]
hardware/laser-cut/bottom_panel.DXF
19.5 x 10.2 in

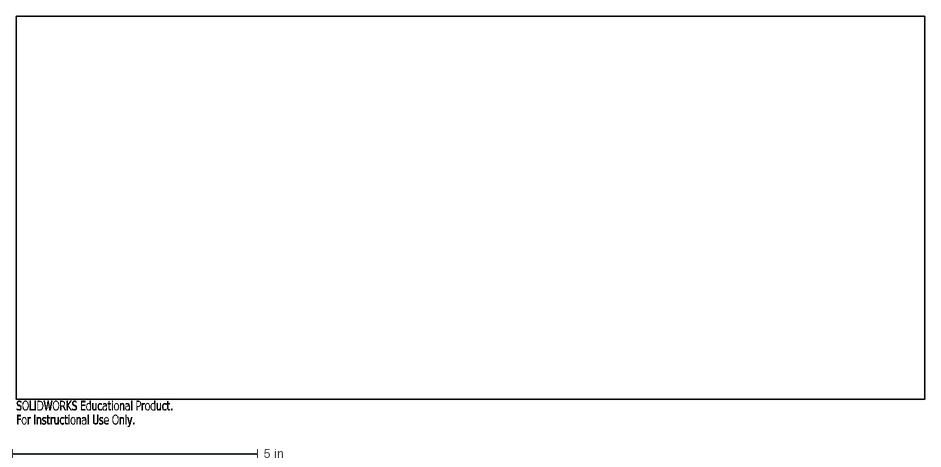
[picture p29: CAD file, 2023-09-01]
hardware/laser-cut/NEW FILES/lid_capture_panel CAP 2.DXF
SOLIDWORKS Educational Product.
For Instructional Use Only.

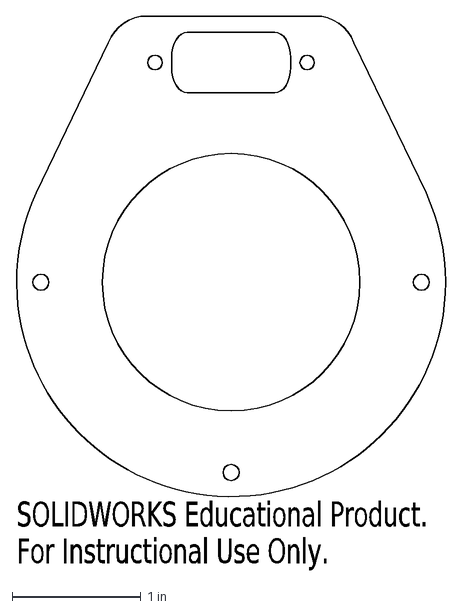
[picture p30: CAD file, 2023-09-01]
hardware/laser-cut/NEW FILES/Speaker Black 8th 02 CAP 2.DXF
SOLIDWORKS Educational Product.
For Instructional Use Only.

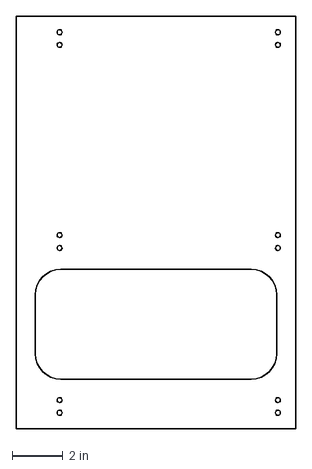
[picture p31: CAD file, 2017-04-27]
hardware/laser-cut/outide_side_panel.DXF
11.0 x 16.2 in

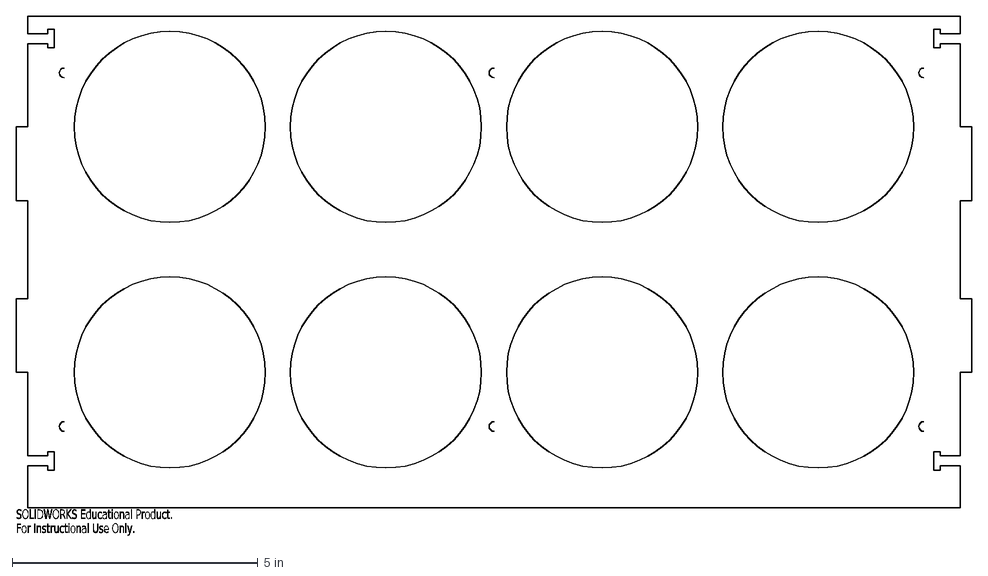
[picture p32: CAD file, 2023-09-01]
hardware/laser-cut/NEW FILES/Top Panel (Revised Pt. 2).DXF
SOLIDWORKS Educational Product.
For Instructional Use Only.

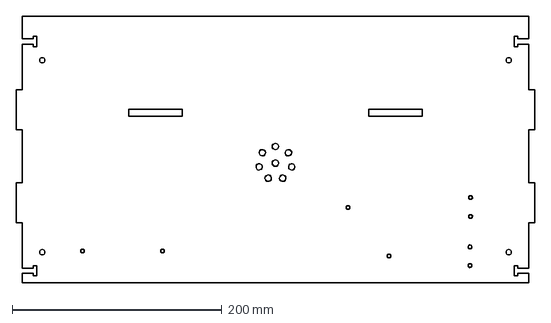
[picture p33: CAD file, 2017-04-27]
hardware/laser-cut/pour_panel.DXF
494.3 x 254.0 mm

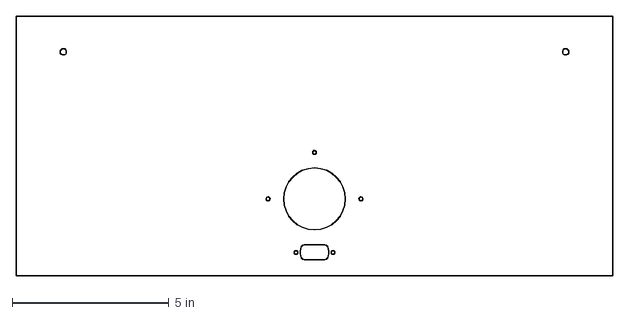
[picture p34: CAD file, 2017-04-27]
hardware/laser-cut/front_panel.DXF
19.0 x 8.25 in

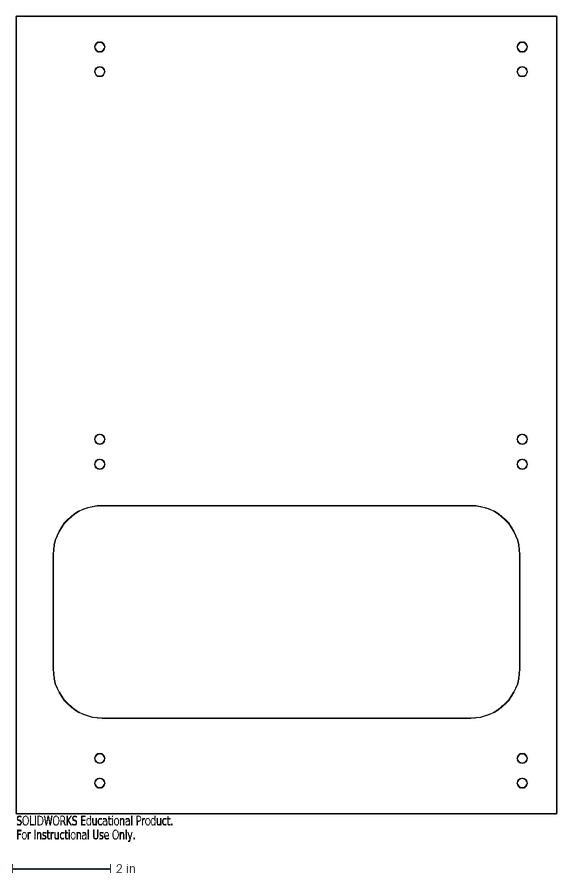
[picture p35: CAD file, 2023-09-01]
hardware/laser-cut/NEW FILES/outside_side_panel CAP 2.DXF
SOLIDWORKS Educational Product.
For Instructional Use Only.

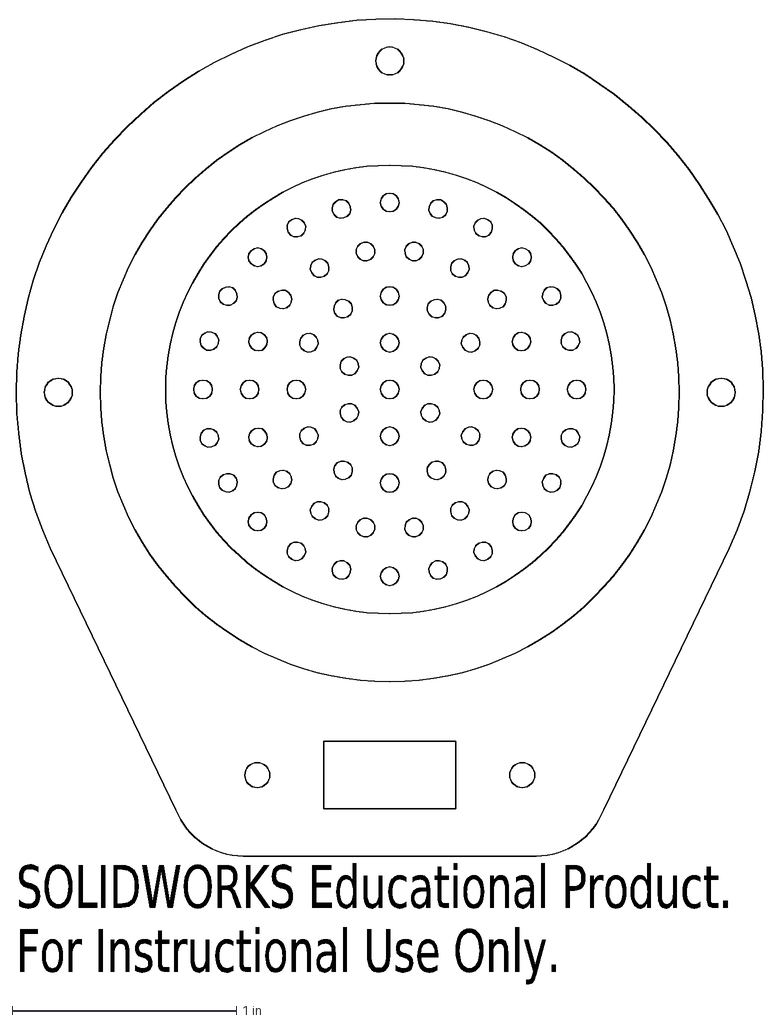
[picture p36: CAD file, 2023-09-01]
hardware/laser-cut/NEW FILES/Speaker Black 8th 01 CAP 2.DXF
SOLIDWORKS Educational Product.
For Instructional Use Only.

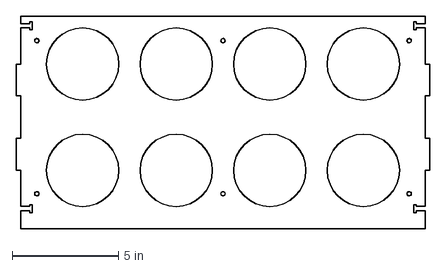
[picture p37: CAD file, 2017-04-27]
hardware/laser-cut/top_panel.DXF
19.5 x 10.0 in

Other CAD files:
hardware/laser-cut/drip_panel.DXF
hardware/laser-cut/NEW FILES/Bottom Panel 2.DXF
hardware/laser-cut/NEW FILES/Top Panel3.DXF
hardware/laser-cut/rear_panel.DXF
hardware/laser-cut/NEW FILES/Bottle Capture Panel CAP 2.DXF
hardware/laser-cut/NEW FILES/BottleCapture (Revised).DXF
hardware/laser-cut/NEW FILES/CupIndicatorPanel CAP 2.DXF
hardware/laser-cut/NEW FILES/Pump Relay Control Panel CAP 2 (Revised PT. 2).DXF
hardware/laser-cut/NEW FILES/Pump Relay Control Panel CAP 2 (Revised) .DXF
hardware/laser-cut/NEW FILES/Top Panel (Revised).DXF
hardware/laser-cut/NEW FILES/drip_panel CAP 2.DXF
hardware/laser-cut/NEW FILES/front_panel CAP 2.DXF
hardware/laser-cut/NEW FILES/inside_side_button_ panel CAP 2.DXF
hardware/laser-cut/NEW FILES/outside_side_button Panel CAP 2.DXF
hardware/laser-cut/NEW FILES/pour_panel CAP2.DXF
hardware/laser-cut/NEW FILES/rear_panel CAP 2 (Revised).DXF
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

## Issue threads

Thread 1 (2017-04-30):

Support for RPi Zero

nikhilnayak98, 2017-04-30:
Is there any support for Raspberry Pi Zero for this demo?

suyashbansal, 2017-05-10:
I think it'll work fine with RP Zero.

oscartprom, 2017-07-25:
The [Assistant developer documentation](https://developers.google.com/assistant/sdk/develop/python/hardware/setup) recommends using the gRPC API instead of the Python library with an RPi Zero and you will have to make some changes around pin numbers, but in theory you should be able to get things working.

Closed 2017-07-25.

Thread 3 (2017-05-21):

Purchase list typo (91772A073)

mscheel, 2017-05-21:
The README references a purchase [list](https://github.com/Deeplocal/mocktailsmixer/blob/master/hardware/bom.pdf).  In row 9 the link is incorrect.

`9 #2-56 X 5/32 in Length Pan Head Philip (91772A073) $0.03 McMaster 4 $0.12 Box of 100 $3.00 https://www.mcmaster.com/#93330a252/=17dak09`

The link should be: https://www.mcmaster.com/#catalog/123/3025/=17q2z03

I think.  It looks like the current link is a copy and paste error as it matches the product number of the item above it (row 8).

Please clarify/correct row 9 of purchase list, thank you!

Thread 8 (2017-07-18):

Incorrect list of items

udaykumarbpatel, 2017-07-18:
The requirement list does not mention anything about the item

#10-32 x 1 inch length ¼ OD standoff.

I ordered the items as listed and now this looks like a new item. I am stuck on Step 1 now.

oscartprom, 2017-07-25:
Is that line item 6 under "Hardware" in the "Additional Optional Materials to Build Assistant Mocktails Mixer" of the [BOM](https://github.com/Deeplocal/mocktailsmixer/blob/master/hardware/bom.pdf)?

udaykumarbpatel, 2017-07-25:
Shouldnt this be added to mandatory list. This isnt additional item since it is needed to make sure the bottle stands properly.

Thanks.

Closed 2017-07-25.

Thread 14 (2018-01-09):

Wrong .dxf for Pour Panel uploaded

darkfile, 2018-01-09:
Hey deeplocal team,

I really enjoyed your drinks on Google I/O last year there is a wrong .dxf for the pour panel (pour_panel.dxf) uploaded. It doesn't fit the other parts dimension wise and has no corresponding tongues for the holes in the back panel. Probably an old design? Could you please upload the right file?

Thank you!

kaihenzler, 2019-01-16:
I'm about to build this Mocktailmixer and I'm experiencing the same issue. Could you please upload the correct file?

fvonberg, 2019-03-05:
@darkfile
The original "pour_panel.dxf" is not wrong, it's just with Millimeters instead of inch as measurement unit.

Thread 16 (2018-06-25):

AttributeError: 'module' object has no attribute 'EmbeddedAssistantStub'

isharaux, 2018-06-25:
I have changed the code according to the latest commits as follows

in ~/embedded-assistant-sdk-python/googlesamples/rpi/__main__.py
`from google.assistant.embedded.v1alpha1 import embedded_assistant_pb2`
to
`from google.assistant.embedded.v1alpha2 import embedded_assistant_pb2`

And the lines,
```
ND_OF_UTTERANCE = embedded_assistant_pb2.ConverseResponse.END_OF_UTTERANCE
DIALOG_FOLLOW_ON = embedded_assistant_pb2.ConverseResult.DIALOG_FOLLOW_ON
CLOSE_MICROPHONE = embedded_assistant_pb2.ConverseResult.CLOSE_MICROPHONE
```
to

```
END_OF_UTTERANCE = embedded_assistant_pb2.AssistResponse.END_OF_UTTERANCE
DIALOG_FOLLOW_ON = embedded_assistant_pb2.DialogStateOut.DIALOG_FOLLOW_ON
CLOSE_MICROPHONE = embedded_assistant_pb2.DialogStateOut.CLOSE_MICROPHONE
```

but when it run the following according to tutorial following error results,

```
(env) pi@raspberrypi:~/embedded-assistant-sdk-python/googlesamples $ python -m rpi
INFO:root:Connecting to embeddedassistant.googleapis.com
Traceback (most recent call last):
  File "/usr/lib/python3.4/runpy.py", line 170, in _run_module_as_main
    "__main__", mod_spec)
  File "/usr/lib/python3.4/runpy.py", line 85, in _run_code
    exec(code, run_globals)
  File "/home/pi/embedded-assistant-sdk-python/googlesamples/rpi/__main__.py", line 440, in <module>
    ret_val = setup_assistant()
  File "/home/pi/embedded-assistant-sdk-python/googlesamples/rpi/__main__.py", line 205, in setup_assistant
    assistant = embedded_assistant_pb2.EmbeddedAssistantStub(grpc_channel)
AttributeError: 'module' object has no attribute 'EmbeddedAssistantStub'

```

NatiDaddy, 2019-04-12:
Damn, I hope I didn't follow you off a cliff. I'm getting the same thing now.
Reading Metadata on the google.assistant.grpc file now about pb2 and will be trying to pick through that.

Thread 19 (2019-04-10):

TypeError: Cannot read property 'metadata' of undefined

aliya16, 2019-04-10:

NatiDaddy, 2019-04-11:
Hello?
This place is pretty dead but I can try to help be of assistance since I'm running into issues as well.
Please let me know what you are having troubles with (specifically step number, input, and results)? I may need your help!

aliya16, 2019-04-12:
Haii, Thankyou for replying. In step number 22 after creating a function. It got verified. But some minutes later it reports the Error written above, cannot read property meta data of undefined.

aliya16, 2019-04-12:
Please do tell how you went through step 23 for deployment.

NatiDaddy, 2019-04-12:
Step 22 or step 23?
Does your function have a green check? Or did it go to a red x with that error?
**Step 22:** I took the 2 files (index and package) and copied them after editing in names. I then selected them both and (I think right clicked them) to send to compressed folder. That compressed folder is the one i zip uploaded.
**Step 23:** Set up an api.ai
Sign into the api.ai console.
From the agents page, click “Create Agent.” **(top left dropdown arrow under diagaflow)**
Give your agent a name. Select “Private” and click “Save.” **(was no option for private)**
Navigate to the Agent Fulfillment page. **(fulfillment a couple rows down from that dropdown arrow. click. Enable webhook....)**
Flip the **Webhook** enabled toggle on, enter the HTTP trigger URL from the Google Cloud Function in the URL field, and click “Save.” **(If you now go back to the cloud function from 22, if you look hard (seriously not that noticeable and easy to just select the wrong http address) you will find a "trigger" tab. That is the HTTP trigger URL you need to put in the webhook url (back in diagaflow). Save (bottom right))**
Navigate to the Agent Settings page. **(Gear icon by the dropdown arrow and name you gave it (Diagaflow))**
Select the “Export and Import” tab and click the “Import from ZIP” button.
Select the ApiAi_MocktailsMixer.zip file from the cloned repository and import. **(in the mocktails mixer master folder i believe)**
Navigate to the Agent **Integrations** page: **(Diagaflow still on left)**
Flip the “Actions on Google” integration on and fill out the form. **(This did not give me the option to flip it. just gave me a selection to test or view or something)**
Select “Authorize” and then “Preview.” Note: Previews are only available for a period of time. Use “Deploy” to register your conversation action with Google. The registration process can take one to two weeks. Read more here.
Test your agent on the Google Home Web Simulator. **(Sometimes it would say my project name and sometimes it wouldn't. I believe I may need to make some changes to my changes (i changed a name within the zipped files).**

Good luck! I'm on California time and am at work right now but I have been updating my issue thread and am at the point where a lot of people have died off here. It seems to be a common issue online so I'm hoping I can get somewhere tonight.

aliya16, 2019-04-12:
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
There is green tick already but this error is shown still.

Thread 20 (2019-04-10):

Out of order? & "bartender-apiai-webhook"? & embedded sdk?

NatiDaddy, 2019-04-10:
I already have a system built running off of arduino mega, LCD, and rotor encoder and wanted to change it to this. I'm running 8 channel relay and have better peristaltic pumps.
This will be for my notes mainly so I will update. Any advice and help is welcome but this place seems pretty much dead.

After weeks of multiple failures and hitting walls I eventually made it through programming the RPi (steps 21-26).

**Mixer Programming**:

I had to start with a section of:
     **Step 24** (due to no option to register device when following order(this also gave me
                          buckets and a better flow through the steps)
          Follow steps in **Getting Started with the Raspberry Pi and Python** (click).
            -Register the Device Model
              -Use the registration UI in the Actions Console to register a device model.
                  -Click the REGISTER MODEL button
                    -add/import (add)
                       -"Register Model" at bottom center

**I then restarted at step 21**making sure I followed all links and through step 24
(directly connected to RPi w/touch screen keyboard and mouse already loaded with Raspian (step 23.10(do noobs so you can "shift" at start to reset and retry))).

**Step 22: Create Google Cloud Function**
     - When I "created a function" I named it to match the name in package.json that is
          compressed with index.js.
           -Fill out the form with the following info:
                Name: bartender-apiai-webhook

**Step 24: link click**
     -Try a different USB for mic if you're getting a full list (and not just 1) when configuring
       .asoundrc
          "hw:#,#" is the proper form.

**Step 26: Clone code repository on RPi and move files into correct location**
26.4:
-If you're reading this, please read the others that have had issues. I've done so many different bartenders I'm starting to mix them all together. I could've sworn I had a "embedded-python folder" in home/pi ("~/") at one point.
Copy files into embedded assistant directory                                       
 **In (env) mode:**
$ cp -r mocktailsmixer/software/rpi /home/pi/env/lib/python3.5/site-packages
$ cd ~/env/lib/python3.5/site-packages/googlesamples
$ python -m googlesamples.rpi.auth_helpers --client-secrets /home/pi/client_secret_############-********.apps.googleusercontent.com
$ python -m googlesamples.rpi

It's working as a google assistant currently. Now I'm figuring out how the 8 ch relay should be hooked up.....

NatiDaddy, 2019-04-11:
Results for step 28:

(env) pi@raspberrypi:~/mocktailsmixer-master $ cd /home/pi/env/lib/python3.5/site-packages/
(env) pi@raspberrypi:~/env/lib/python3.5/site-packages $ python -m googlesamples.rpi
Traceback (most recent call last):
  File "/usr/lib/python3.5/runpy.py", line 193, in _run_module_as_main
    "__main__", mod_spec)
  File "/usr/lib/python3.5/runpy.py", line 85, in _run_code
    exec(code, run_globals)
  File "/home/pi/env/lib/python3.5/site-packages/googlesamples/rpi/__main__.py", line 21, in <module>
    from google.cloud import pubsub
  File "/home/pi/env/lib/python3.5/site-packages/google/cloud/pubsub.py", line 19, in <module>
    from google.cloud.pubsub_v1 import PublisherClient
  File "/home/pi/env/lib/python3.5/site-packages/google/cloud/pubsub_v1/__init__.py", line 17, in <module>
    from google.cloud.pubsub_v1 import types
  File "/home/pi/env/lib/python3.5/site-packages/google/cloud/pubsub_v1/types.py", line 20, in <module>
    from google.iam.v1 import iam_policy_pb2
  File "/home/pi/env/lib/python3.5/site-packages/google/iam/v1/iam_policy_pb2.py", line 17, in <module>
    from google.iam.v1 import policy_pb2 as google_dot_iam_dot_v1_dot_policy__pb2
  File "/home/pi/env/lib/python3.5/site-packages/google/iam/v1/policy_pb2.py", line 366, in <module>
    from grpc.beta import implementations as beta_implementations
  File "/home/pi/env/lib/python3.5/site-packages/grpc/beta/implementations.py", line 22, in <module>
    from grpc import _auth
  File "/home/pi/env/lib/python3.5/site-packages/grpc/_auth.py", line 17, in <module>
    from concurrent import futures
  File "/home/pi/env/lib/python3.5/site-packages/concurrent/futures/__init__.py", line 8, in <module>
    from concurrent.futures._base import (FIRST_COMPLETED,
  File "/home/pi/env/lib/python3.5/site-packages/concurrent/futures/_base.py", line 381
    raise exception_type, self._exception, self._traceback
                        ^
SyntaxError: invalid syntax

NatiDaddy, 2019-04-12:
Update:
The last error i ended up just making them 3 raises.

Now:

AttributeError: module 'google.assistant.embedded.v1alpha1.embedded_assistant_pb2' has no attribute 'EmbeddedAssistantStub'

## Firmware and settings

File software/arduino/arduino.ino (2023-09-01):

/*
 * Basic Description of firmware functionality:
 * Mixology Pushbutton state is constantly monitored. When pressed, we start "conversational user experience"
 * animation and send a "button" message to the PI. We remain in this state until either:
 *   - we receive a bottle command to turn on a relay from PI -OR-
 *   - we receive an "inactive state" message (o!) from PI
 * If we send a button pressed message to PI, but don't receive an 'a!" confirmation and also don't receive a relay on message
 * within 30 seconds, we can assume a fault and will being reading the button pin again.
 * All commands from PI are terminated with an '!'
 * Bottle commands include:
 *    - 'b' (bottle command), 0-7 (bottle index number), 'r' (relay on) or 'l' (relay off), '!' (termination statement)
 * Conversational User State messages either
 *    - 'a!' => ACTIVE
 *    - 'o!'  => INACTIVE
 * LED animation rate controlled by _LEDrate variable -> default value is 10 (milliseconds between updates)
 * LED animation brightness MIN and MAX controlled by BASE_BRIGHTNESS and RAISED_BRIGHTNESS constants
 *    
 * Bottle numbers are 0-7 _indexed.
 * PIN 3 =  relay/bottle 0
 * PIN 4 =  relay/bottle 1
 * PIN 5 =  relay/bottle 2
 * PIN 7 =  relay/bottle 3
 * PIN 8 =  relay/bottle 4
 * PIN 9 =  relay/bottle 5
 * PIN 10 = relay/bottle 6
 * PIN 11 = relay/bottle 7
 * 
 * PIN 2 = pushbutton switch
 * PIN 6 = NeoPixel LED rings (with 330 Ohm series resistor)
 **********************************************************************
 *OTHER NOTES:
 *relay unit in this version is active LOW, so operation is logically reversed (LOW write to a digital pin turns
 *relays ON). 
 */

#include <Adafruit_NeoPixel.h>
#ifdef __AVR__
  #include <avr/power.h>
#endif

#define BUTTON_PIN 2 // pin connected to the arcade style pushbutton

#define NUM_BOTTLES 8
#define NUM_RINGS 9
#define NEO_PIN 6
#define BASE_BRIGHTNESS 50
#define RAISED_BRIGHTNESS 200
#define MAX_CMD_SIZE 8
#define PIX_RING_SIZE 24
#define NUM_PIX (PIX_RING_SIZE*NUM_RINGS)
#define CUX_LED_INDEX (PIX_RING_SIZE*NUM_BOTTLES) //location of conversational user experience LED ring in series

// Parameter 1 = number of pixels in strip
// Parameter 2 = Arduino pin number (most are valid)
// Parameter 3 = pixel type flags, add together as needed:
//   NEO_KHZ800  800 KHz bitstream (most NeoPixel products w/WS2812 LEDs)
//   NEO_KHZ400  400 KHz (classic 'v1' (not v2) FLORA pixels, WS2811 drivers)
//   NEO_GRB     Pixels are wired for GRB bitstream (most NeoPixel products)
//   NEO_RGB     Pixels are wired for RGB bitstream (v1 FLORA pixels, not v2)
//   NEO_RGBW    Pixels are wired for RGBW bitstream (NeoPixel RGBW products)
Adafruit_NeoPixel strip = Adafruit_NeoPixel(NUM_PIX, NEO_PIN, NEO_GRB + NEO_KHZ800);

// IMPORTANT: To reduce NeoPixel burnout risk, add 1000 uF capacitor across
// pixel power leads, add 300 - 500 Ohm resistor on first pixel's data input
// and minimize distance between Arduino and first pixel.  Avoid connecting
// on a live circuit...if you must, connect GND first.

/*
 * Array to hold incoming serial commands
 */
char cmd[MAX_CMD_SIZE];
uint16_t _index = 0;

char _cuxState = 'o'; // cux = conversational user experience state options:
                      // 'o' == OFF 
                      // 'a' == ACTIVE 
                      // 'd' == DRINK BEING MADE
                     

// in order of bottles (controlled by relays) 
//NOTE: NOT SEQUENTIAL!! be careful of pin 2 and 6!
uint8_t _relayPins[] = { 3, 4, 5, 7, 8, 9, 10, 11 }; //note: pin 6 used for the neoPixel LEDs
                                                     //note: pin 2 used for pushbutton!!!
bool _bottleStatus[] = { 0, 0, 0, 0, 0, 0,  0, 0  }; //local status for bottle state LED
bool _cuxDir=1;        //sets direction of LED animation (1=increase brightness, 0=decrease brightness)
uint8_t _iterNum=0;    //variable to set LED brightness in animations
uint8_t _LEDrate = 10; //animation rate: use caution this is a program delay between LED updates, affects everything

uint32_t buttonTime = 0;  //used to store clock time for pushbutton switch timing
uint16_t debounce = 1000; //debounce+delay time used for input switch debounce and to delay frequency of valid reads
                          //**NOTE** this is not a program delay: time compared here against millis(), so a longer
                          //timeout can be used here without adversely affecting other functionality
                          
uint32_t timeOut = 30000; //if a drink is not made 30 seconds after button is pressed, start reading the button again.


void setup() {
  // start serial
  Serial.begin(9600); //open serial communication w/rasperry pi at 9600 baud rate

  // set pin modes for relays; set pins to HIGH (off) to start
  for (uint8_t i = 0; i < NUM_BOTTLES; i++) {
    pinMode(_relayPins[i], OUTPUT);
    digitalWrite (_relayPins[i], HIGH); //relay unit is active LOW, so HIGH write turns OFF relays
  }
  //declare pin arcade button is connected to to be an input
  pinMode (BUTTON_PIN, INPUT_PULLUP);
  // start neopixel strip and turn pixels off
  strip.begin();
  allOff();
}

void loop() {
  //if we're in conversational user state, but a drink recipe has not started 30 seconds after button press, return to inactve state
  if (_cuxState == 'a' && ((millis()-buttonTime)>timeOut)){
    _cuxState = 'o';
    Serial.println ("TimeOut reached, returning to INACTIVE state. Reading the switch again."); Serial.println();
  }
  //if we're in inactive state, constantly read the pushbutton switch pin.
  if (_cuxState == 'o'){
    checkButton();
  }
  // check for available serial data
  if (Serial.available() > 0) {
    // append char to command
      cmd[_index] = Serial.read();
    // if character is NOT command terminator
    if (cmd[_index] != '!' || '\0' ) {
      // increment command _index
      _index++;
    }
  }
  // else process entire command
  else {
      // was command valid? default to yes
      uint8_t cmdValid = 1;
      //////////////////////////////////////////////////////////////////////////////////////////////////////
      // bottle commands
      //////////////////////////////////////////////////////////////////////////////////////////////////////
      if (cmd[0] == 'b') {
        // parse command
        char temp[2] = { cmd[1], '\0' };
        uint8_t bottleNum = atoi(temp); //atoi interprets string content as integer, returns integer value
        // change state based on action
        switch (cmd[2]) {
          case 'r':
            // turn on relay
            digitalWrite(_relayPins[bottleNum], LOW); //relays active LOW, this turns ON the relay
            Serial.print ("relay index # "); Serial.print (bottleNum); Serial.println (" is ON!");
             _bottleStatus[bottleNum]=1; //set status to active for bottle animation
             _cuxState = 'd'; //stay in "Drinks being made" state until all relays are off
            break;
          case 'l':
            // turn off relay
            digitalWrite(_relayPins[bottleNum], HIGH); //relays active HIGH, this turns OFF the relay
            Serial.print ("bottle index # "); Serial.print (bottleNum); Serial.println (" Relay is OFF!");
            _bottleStatus[bottleNum]=0; //set status to inactive to stop bottle animation
            checkMachineStatus();
            break;
          default:
            cmdValid = 0;
            break;
        }
        updateLEDs();
      }
      //////////////////////////////////////////////////////////////////////////////////////////////////////
      // ui commands
      //////////////////////////////////////////////////////////////////////////////////////////////////////
      else if  (cmd[0] == 'a') {
        // set conversational user state to active
        _cuxState = cmd[0];
        _iterNum = 0;
        Serial.println ("Conversational User State is ACTIVE!");
        updateLEDs();
      }
      // set conversation user state to inactive
      else if (cmd[0] == 'o'){
        _cuxState = cmd[0];
        Serial.println ("Conversational User State is NOT active.");
        //turn off all relays and LEDs; begin listening for button presses
        resetMachine(); //turn off any LEDs or relays that are active, clear bottle status array
      }
      else{
        cmdValid = 0;
      }
      //////////////////////////////////////////////////////////////////////////////////////////////////////
      // send response
      //////////////////////////////////////////////////////////////////////////////////////////////////////
      if (cmd[0] != '\0'){
        if (cmdValid == 1) {
          Serial.println("OK: Valid Message Received:");
          uint8_t _index = 0;
          for (uint8_t i=0; i<MAX_CMD_SIZE; i++){
            if (cmd[i] != '\0'){Serial.print(cmd[i]); Serial.print("   ");}
          }
          Serial.println();
        } else if (cmdValid == 0) {
          Serial.println("ERR: Invalid Message Receivd:");
          for (uint8_t i=0; i<MAX_CMD_SIZE; i++){
            if (cmd[i] != '\0'){Serial.print(cmd[i]); Serial.print("   ");}
          }
          Serial.println();
        } else {
          Serial.println("?");
        }
      }
      //////////////////////////////////////////////////////////////////////////////////////////////////////
      // reset the command buffer and _index
      //////////////////////////////////////////////////////////////////////////////////////////////////////
      resetCmd();
  }
  delay(10);
}

//////////////////////////////////////////////////////////////////////////////////////////////////////////
//reset CMD array, get ready for new data
//////////////////////////////////////////////////////////////////////////////////////////////////////////
void resetCmd() {
  for (uint16_t i = 0; i < MAX_CMD_SIZE; i++) {
    cmd[i] = '\0';
  }
  _index = 0;
}

//////////////////////////////////////////////////////////////////////////////////////////////////////////
//interrupt service routine (isr) to monitor pushbutton presses
//////////////////////////////////////////////////////////////////////////////////////////////////////////
void checkButton() {
  if (digitalRead(BUTTON_PIN)==0 && (millis()-buttonTime)>debounce){
    buttonTime=millis();
    Serial.println ("Message sent:");
    Serial.println ("button"); //msg sent to PI to alert that conversational user experience has begun
    Serial.println ();
    //_cuxState = 'a'; //add this for debug purposes, during normal operation PI is responsible for sending this command
  }
}

//////////////////////////////////////////////////////////////////////////////////////////////////////////
//Turn off all LEDs
//////////////////////////////////////////////////////////////////////////////////////////////////////////
void allOff() {
  for (uint16_t px = 0; px < strip.numPixels(); px++) {
    strip.setPixelColor(px, 0, 0, 0);
  }
  strip.show();
}

//////////////////////////////////////////////////////////////////////////////////////////////////////////
//LED animation routine
//////////////////////////////////////////////////////////////////////////////////////////////////////////
void updateLEDs(){
  //if we're in "Conversational User Experience == ACTIVE" adjust Speaker LED ring LED animation
  if (_cuxState == 'a'){
    for (uint8_t px = 0; px < 24; px++) {
      strip.setPixelColor((CUX_LED_INDEX+px), BASE_BRIGHTNESS, BASE_BRIGHTNESS, BASE_BRIGHTNESS);
    }
  }
  //otherwise, lets make sure the Speaker LED ring is off
  else{
    for (uint8_t px = 0; px < 24; px++) {
      strip.setPixelColor((CUX_LED_INDEX+px), 0,0,0);
    }
  } 
  //if a bottle relay is active, adjust bottle LED ring animation
  for (uint8_t i=0; i<NUM_BOTTLES; i++){
    for (uint8_t j=0; j<PIX_RING_SIZE; j++){
        strip.setPixelColor(((i*PIX_RING_SIZE)+j), (BASE_BRIGHTNESS*_bottleStatus[i]),(BASE_BRIGHTNESS*_bottleStatus[i]),(BASE_BRIGHTNESS*_bottleStatus[i]));
    }
  }
  strip.show(); //update the pixels
}

//////////////////////////////////////////////////////////////////////////////////////////////////////////
//Check Machine Status:
//when we turn off a relay, lets see if any other relays are active. if not, let's set the unit to
//inactive (cux == o) and begin waiting for button presses
//////////////////////////////////////////////////////////////////////////////////////////////////////////
void checkMachineStatus(){
  uint8_t _flag = 0;
  for (uint8_t i=0; i<NUM_BOTTLES; i++){
    _flag = (_flag + _bottleStatus[i]);
  }
  if (_flag==0){
    _cuxState = 'o'; //set conversational user state to inactive
    updateLEDs();
  }
}

//////////////////////////////////////////////////////////////////////////////////////////////////////////
//Reset Machine:
//if we receive a "conversational user state inactive" message from PI, turn off any active LEDs and Relays
//////////////////////////////////////////////////////////////////////////////////////////////////////////
void resetMachine(){
  allOff(); //turn off LEDs if any of them are on...
  for (uint8_t i=0; i<NUM_BOTTLES; i++){
     _bottleStatus[i] = 0; //set bottle status to OFF
     digitalWrite(_relayPins[i], HIGH); //turn off the corresponding bottle relay (if it was on)
  }
  buttonTime=millis();
}

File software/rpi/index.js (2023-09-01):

const { SpeechComponent } = require('./speech');
const { DialogComponent } = require('./dialog');
const path = require('path');
const { SerialPort } = require('serialport')


const port = new SerialPort(
  { path: '/dev/ttyACM0', baudRate: 9600 },
  function (err) {
    if (err) {
      console.error(err);
      return ('Error: ', err.message);
    }
  }
);

port.on("open", () => {
  port.write("o!");
  console.log("reseting");
});

port.on("error", (err) => {
  console.error("Serial error:", err);
});




// remove text to speech because we didn't use it
const textToSpeech = require('@google-cloud/text-to-speech');
const fs = require('fs');
const util = require('util');
const client = new textToSpeech.TextToSpeechClient();

let keyword = '';

process.env['GOOGLE_APPLICATION_CREDENTIALS'] = path.join(
  process.cwd(),
  'secretkey.json'
)
function processTranscript(transcript) {
  let keyWords = ['mechanical', 'lavender', 'mud', 'mango', 'strawberry'];
  for (let i = 0; i < keyWords.length; i++) {
    let kw = keyWords[i]
    if (transcript.includes(kw))
      return kw
  }

  return "nodrink"


}


let transcript = '';
let word = false;

// Create new speech and dialog instances...
const Speech = new SpeechComponent();
const Dialog = new DialogComponent();

// Example of speech
function buttonCallback(data) {

  //dont need .to string = redundant
  if (data.toString().startsWith("button")) {
    convertTextToMp3();
    Speech.startRecording();
    setTimeout(() => {
      Speech.stopRecording();
      port.write("o!"); console.log("sending:", "o!");
      transcript = Speech.getResult();
      console.log(transcript);
      word = transcript.includes("mango");
      // console.log(`FIRST RECORDING: ${transcript}`);
      // console.log(`${word}`);
      keyword = processTranscript(transcript);
      //console.log(keyword);
      keyWordToArduino(keyword);
    }, 10000);
  }
}

let serialBuffer = "";

function handleSerial(data) {
  serialBuffer += data.toString();
  if (serialBuffer.indexOf("\n") != -1) {
    let sb = serialBuffer.slice(0, serialBuffer.indexOf("\n"));
    console.log("Serial recieved: ", sb.toString());

    // if statement redundant
    if (sb.startsWith("button")) {
      buttonCallback(sb);
      port.write("a!"); console.log("sending:", "a!");
    }
    serialBuffer = serialBuffer.slice(serialBuffer.indexOf("\n") + 1);
  }
}

port.on('data', handleSerial)

// Example of dialog
Dialog.checkForDrink('Example text we would want to check...');

async function convertTextToMp3() {
  const text = "Welcome to the Gizmos Mocktail Mixer."

  const request = {
    input: { text: text },
    voice: { languageCode: 'en-US', ssmlGender: 'FEMALE' },
    audioConfig: { audioEncoding: 'MP3' },
  };

  const [response] = await client.synthesizeSpeech(request)

  const writeFile = util.promisify(fs.writeFile)

  await writeFile("output.mp3", response.audioContent, 'binary')

  //console.log('text to speech working');
  await writeFile("strawberry.mp3", response.audioContent, 'binary')

  // console.log('text to speech working');
}

convertTextToMp3()

function keyWordToArduino(keyword) {

  if (keyword.includes('mango')) {

    //open b0 lemonade after 1 second of button press
    setTimeout(() => {
      port.write("b0r!"); console.log("sending:", "b0r!");
      // open b7 mango concentrate after 2 seconds
      setTimeout(() => {
        port.write("b7r!"); console.log("sending:", "b7r!");
      }, 2000)
      // close b7 mango concentrate after 44 seconds
      setTimeout(() => {
        port.write("b7l!"); console.log("sending:", "b7l!")
      }, 44000);
      // turn off b0 lemonade after 132 seconds
      setTimeout(() => {
        port.write("b0l!"); console.log("sending:", "b0l!")
      }, 132000);

      //-----

      setTimeout(() => {
        port.write("b7l!"); console.log("sending:", "b7l!")
      }, 45000);

      setTimeout(() => {
        port.write("b0l!"); console.log("sending:", "b0l!")
      }, 133000);

    }, 1000)
  }


  else if (keyword.includes('mechanical')) {
    //open b1 lemonade after 1 second
    setTimeout(() => {
      port.write("b1r!"); console.log("sending:", "b1r!");
      //open b5 watermelon after 2 seconds
      setTimeout(() => {
        port.write("b5r!"); console.log("sending:", "b5r!");
      }, 2000)
      // after 44 seconds close b1 lemonade
      setTimeout(() => {
        port.write("b1l!"); console.log("sending:", "b1l!")
        //after one second of b1 close, close b5 watermelon
        setTimeout(() => {
          port.write("b5l!"); console.log("sending:", "b5l!")
        }, 1000);
      }, 44000);
      //------
      setTimeout(() => {
        port.write("b1l!"); console.log("sending:", "b1l!")
      }, 46000);

      setTimeout(() => {
        port.write("b5l!"); console.log("sending:", "b5l!")
      }, 47000);


    }, 1000)
  }

  else if (keyword.includes('mud')) {

    //open b2 lemonade after 1 second
    setTimeout(() => {
      port.write("b1r!"); console.log("sending:", "b1r!");
      //open b3 iced tea after 2 seconds
      setTimeout(() => {
        port.write("b3r!"); console.log("sending:", "b3r!");
      }, 2000)
      // after 44 seconds close b2 lemonade
      setTimeout(() => {
        port.write("b1l!"); console.log("sending:", "b1l!")
        //after one second of b2 close, close b3 iced tea
        setTimeout(() => {
          port.write("b3l!"); console.log("sending:", "b3l!")
        }, 1000);
      }, 44000);

    }, 1000)
  }

  else if (keyword.includes('lavender')) {

    //open b1 lemonade after 1 second
    setTimeout(() => {
      port.write("b2r!"); console.log("sending:", "b2r!");
      //after two seconds open b6 lavender syrup

      setTimeout(() => {
        port.write("b2l!"); console.log("sending:", "b2l!")
      }, 144000);

    }, 1000)
  }

  else if (keyword.includes('strawberry')) {

    //open b4 strawberry lemonade
    setTimeout(() => {
      port.write("b6r!"); console.log("sending:", "b6r!");

      //after 176 seconds close b4
      setTimeout(() => {
        port.write("b6l!"); console.log("sending:", "b6l!")

      }, 176000)

      setTimeout(() => {
        port.write("b6l!"); console.log("sending:", "b6l!")
      }, 178000);
    }, 1000)
  }

  else {

    ("Error, try again.")
  };

}

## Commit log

2017-04-27 initial commit - yay
    [arduino_bottom_plate.DXF, arduino_top_plate.DXF, bottle_capture_panel.DXF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]
2023-09-01 Feature/gizmology update (#21)
    * init
    * init
    * aren and em 7-18
    * Delete localsdk3-b447e60b51d1.json
    * Cleanup, making classes
    * Updating with tiny note
    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
    [Bottle Capture Panel CAP 2.DXF, BottleCapture (Revised).DXF, Bottom Panel 2.DXF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]
